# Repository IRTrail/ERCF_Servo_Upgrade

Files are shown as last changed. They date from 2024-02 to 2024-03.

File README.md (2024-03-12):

# Promodeler ERCF Servo Upgrade
#### Using the ProModeler DS105CLHV Servo  
##### Disclaimer: I am not an affiliate of ProModeler and I don't get any sort of compensation from ProModeler for this. I just like their stuff. It's some of the best on the market and far more reasonably priced than servos of competing quality.
### [Click here for more info on the servo or to buy](https://www.promodeler.com/DS105CLHV)

## Pictures
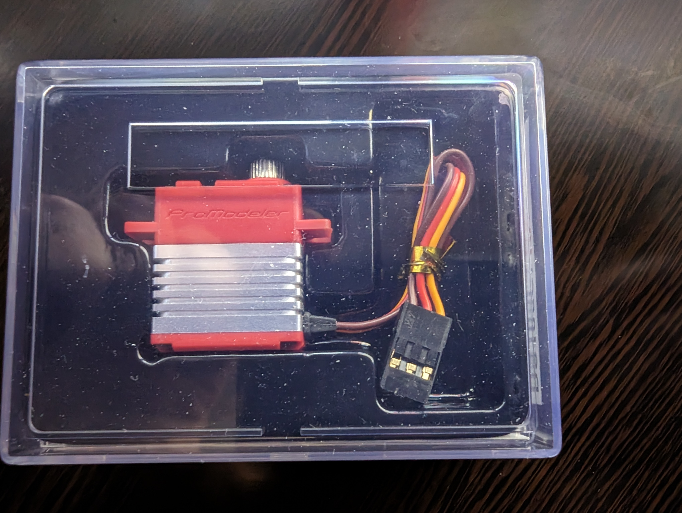
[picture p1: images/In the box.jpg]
In the box.jpg

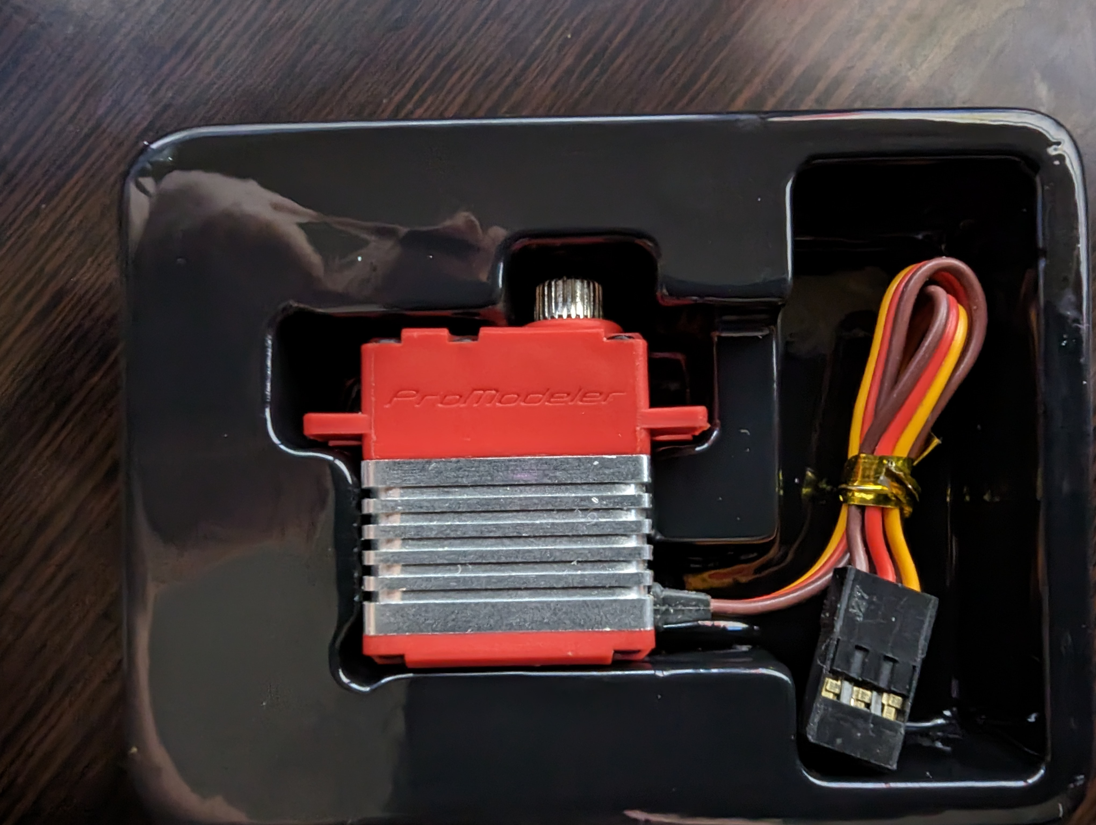
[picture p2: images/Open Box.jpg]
Open Box.jpg

## Why do you *need* it?  
- Well, because it is a high quality servo that pretty much blows others out of the water...at a reasonable price.  
-- Most other high-end servos like this are double (or more) cost. Others aren't made by a guy who answers emails.  
-- Others aren't made by a guy that actually does RC and knows how much quality matters.  
-- Others aren't made by John Beech, engineer, electronics guru, and all-around good guy.  
- The specs are listed under the `Specifications` tab on the link above. You'll notice, that for the input voltage, the ProModeler servo has **46%** more torque at 4.8V than the paltry Savox offering. The MG90S is simply a wet tissue in comparison.  
- This servo has a CNC aluminum housing. How cool is that?  
- This servo has a 25T spline, which is compatible with most servo arms, not that the ERCF uses standard servo arms, but standardization is good for the end user.  
- It uses a...wait for it...M3 servo screw. No more hunting for a M2.5, M2, M-whatever that only fits your specific servo because you dropped the only one in existence into the ethereal plane which swallows important screws, 10MM sockets, and single socks for all eternity. Just grab another M3 button head from your stash and laugh at the infernal depths of screw stealing madness.  
- It is **quiet**. Seriously, compared to a MG90s, this thing whispers instead of coughs like your old crazy uncle that smokes too much.
- ProModeler servos are used by the military. [They're also used to aim high precision lasers.](https://www.promodeler.com/profiles/NPL-ProModeler-and-steering-lasers)  
-  
## Important notes:
##### Don't back drive your servo.
Seriously just don't. Back driving is moving the servo arm by hand. It's not good for the servo. This servo has a 480:1 gear ratio and back driving can impart huge stresses on the gear train, not to mention spinning the servo motor at insane speeds. Back EMF could be a thing if you have it plugged into the MMU board already, just like moving the stepper motors for the X, Y, and Z axes will eventually fry your MCU.
The ProModeler website is full of warnings about it. It can **VOID YOUR WARRANTY**. So just don't. It's not a great idea for any servo, if we're honest. So don't. Have I mentioned...don't back drive your servo?
## Great. What other stuff do I need?
Good question. You'll need the following:
1) [A servo arm](STL/Servo%20Arm%20ProModeler.STL). This servo has 25T splines and neither of the other available servo arms work. So, I made one for you. Depending on your printer tolerances, it will be from a perfect fit to impossible to install. Tweak your extrusion modifier and print another if the fit isn't correct.
-- **Print the servo arm with very thin layers**. I usually print mine with 0.12mm layers and shoot for 0.18mm first layer. This helps define the spline better and get a more perfect fit.
2) A servo extension. ProModeler has several lengths [here](https://www.promodeler.com/extensions) and guess what. They have a locking tab. How cool is that? Order one when you order your servo. Yes, you can craft your own, but why crimp another connection when you can let someone else?
-- A good approximation of the extension length needed is (315 + (number of gates * 23.05)) * 1mm and round to the nearest 10mm.  
(I currently have a 6 gate ERCF in V2 spec. The numbers below are for reference only and not tested)

| Gates | Length (mm) | Length (in) |
|---|---|---|
| 4 | 410 | 16.14 |
| 6 | 450 | 17.72 |
| 8 | 500 | 19.69 |
| 12 | 590 | 23.23 |

3) [A servo mount](STL/Servo%20Mount%20Promodeler.STL). This servo has slightly different geometry from either the MG90S or the Savox SH-0225MG, and thus needs a new mount.
4) [A new idler block](STL/Linear%20Axis%20Idler%20Block%20ProModeler.STL). The pocket for the servo has been deepened by 2.2mm to accommodate the extra badassitude of the ProModeler.
5) The wire bracket for the selector cart. You really don't want to snip the wire on such a nice servo do you? I didn't either. Use a different selector bracket so your servo wire doesn't need snipped. [The one from GNeu42 looks promising.](https://github.com/Enraged-Rabbit-Community/ERCF_v2/tree/master/User_Mods/Gneu42/Selector_Drag_chain_Anchor_with_servo_connectors) 
6) A couple 2mm self tappers or 2mm socket head cap screws. The important thing here is they can't be longer than 5mm or they'll poke through and prevent the springiness of the Springy servo mount from springing. If you don't have something 5mm or shorter, file them down, or hit them with a Dremel. Just don't do it with the servo in place and screw up the finish on your new blingified servo.
## So, how do I install it?
Well, pretty much like you installed the other servo options. Although, you'll need to replace the idler block as well. Make sure you don't put the servo arm on before powering up the servo. You'll want to leave it off. FIrst, put the servo in the UP position. **Only after the servo is in the up position should you install the arm** with the leg as close to the servo housing as possible. But **make sure it isn't installed on initial power up** so the servo doesn't stall before it's set up in Happy Hare.

Note: It's ok to pre-install the servo arm on the servo to make it fit well before the initial power up, just remember to remove it before power up.  

According to the specs, this servo has a 150° range based on 800-200 microsecond pulsewidth. So, you'll want to adjust those in `mmu_hardware.cfg`.
  

Calibrate the servo as normal and set the springy bolt to suit. You don't want it so tight it stalls the servo. Just enough to engage the gears firmly. For servo calibration routine, see [Page 127 in the ERCF V2 build manual](https://github.com/IRTrail/ERCF_v2/blob/master/Documentation/ERCF_v2_Manual.pdf)  and [Happy Hare servo calibration](https://github.com/moggieuk/Happy-Hare/blob/main/doc/calibration.md#step-2-calibrate-your-servo).  

For reference only, my numbers are 30 for the up position and 90 for the down position using Thumper Blocks and the pulsewidths above.  
  

One person said their servo worked backward from the Savox, which makes sense when looking at the suggested values for the Savox vs. the MG90s. If yours seems reversed, just reverse the numbers in the config, then tune from there.
I haven't had the Triple Decky blocks with this servo, so I don't have an example for those.

##### Here's a picture of it all nestled into place making the ERCF happy:
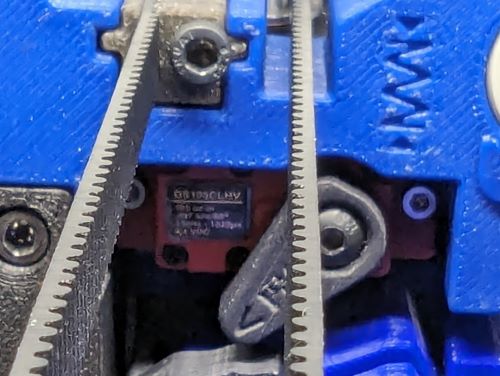
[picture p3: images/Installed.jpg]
  
Yeah, it's really hard to get a nice picture of it installed.
## Ok. What else have you got for me?
Well, since you asked...[there's a total bling version made from solid brass](https://www.promodeler.com/DS125CLHV-BM).

#### Hit me up on discord if you have any questions or suggestions @Silverback_Attack.



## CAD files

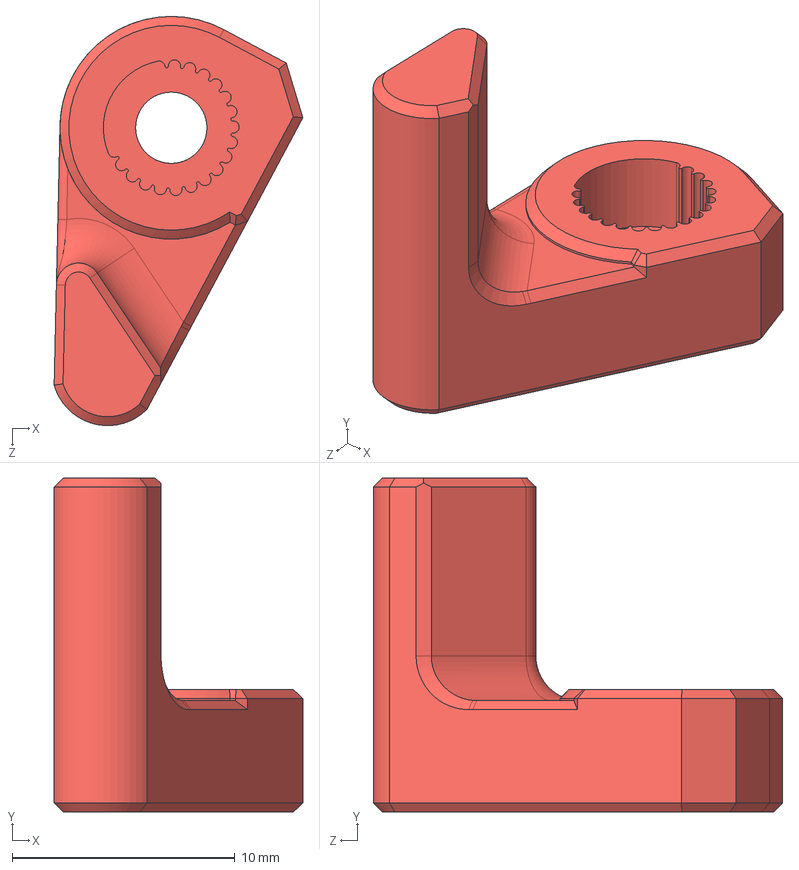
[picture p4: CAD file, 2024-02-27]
CAD/Servo Arm ProModeler.STEP
11.2 x 15.0 x 18.4 mm

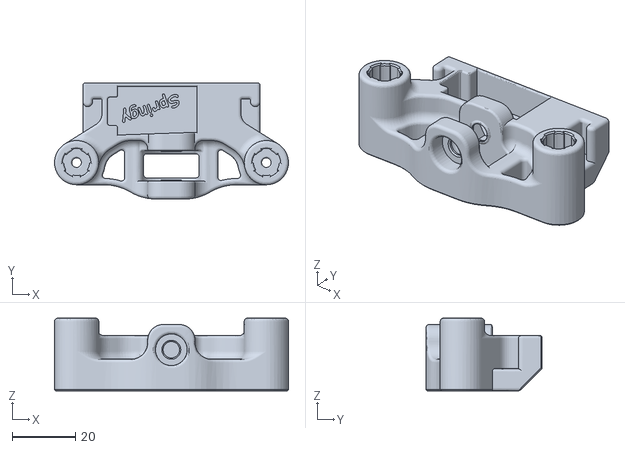
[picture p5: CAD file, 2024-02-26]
STL/Linear Axis Idler Block ProModeler.STL
74.0 x 36.7 x 23.0

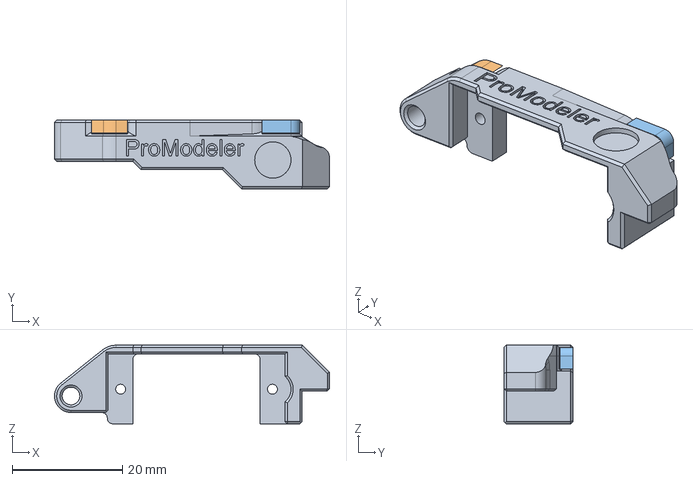
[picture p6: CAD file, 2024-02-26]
CAD/Servo Mount ProModeler.step
50.0 x 12.5 x 14.3 mm

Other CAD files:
CAD/Idler Block ProModeler.step
STL/Servo Arm ProModeler.STL
STL/Servo Mount Promodeler.STL

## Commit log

2024-02-26 Upload CAD and STLs
    [Idler Block ProModeler.step, Linear Axis Idler Block ProModeler.STL, Servo Arm ProModeler.STEP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]
2024-02-27 Added images and updated CAD files
    [Servo Arm ProModeler.STEP, Servo Arm ProModeler.STL]
